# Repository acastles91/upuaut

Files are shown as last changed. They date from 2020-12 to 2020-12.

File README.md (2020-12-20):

# upuaut
Upuaut KiCad Project

### Explicación
El proyecto se abre desde el archivo `upuaut_2Nils.pro`. El esquemático correspondiente es `upuaut_2Nils.sch`. La nomenclatura es un desorden porque empecé a hacer el proyecto antes de saber de version control y no he reordenado todo, cuando sepa mejor por donde coger lo haré de ceros. 

En el esquemático se puede ver arriba a la izquierda el Teensy 3.2 que controla todo. Las conexiones están hechas sobre todo con `labels`. `START-STOP`, `DIRECTION-SWITCH`, `CAPTURE` y `SPEED-SELECT` son botones con interrupt. El código lo puede ver en [este repositorio](https://github.com/acastles91/Upu). El loop es en términos generales algo así:

```
volatile Request requestStream = checkInputStreamOF(Serial, prevRequest);
  if(requestStream != prevRequest){
    switchStateOF(requestStream,
                prevRequest, 
                stepperObj, 
                stepControlObj, 
                rotateControlObj, 
                sensorObj, 
                rotaryObj, 
                openCelluloidObj, 
                motorObj, 
                bounceSensor,
                leds,
                encoderObj,
                bounceEncoButton,
                triggerTimerObj,
                modeObj,
                debouncers,
                stateObj,
                bounceStartStop);
    prevRequest = requestStream;
  }

    volatile Request requestButton = checkInputButtonsOF(debouncers, prevRequest);
    if(requestButton != prevRequest){
    switchStateOF(requestButton,
                prevRequest,
                stepperObj, 
                stepControlObj, 
                rotateControlObj, 
                sensorObj, 
                rotaryObj, 
                openCelluloidObj, 
                motorObj, 
                bounceSensor,
                leds,
                encoderObj,
                bounceEncoButton,
                triggerTimerObj,
                modeObj,
                debouncers,
                stateObj,
                bounceStartStop);
     }
```
Escribí una clase que se llama `Request`. Las funciones `checkInputStreamOF()` y `checkInputButtonsOF()` tienen como `return value` un `Request`. Existe de antes un `Request` llamado `prevRequest`. Este `Request` es el valor del último `Request` del cual el programa tiene conocimiento. Si las funciones dan como `return value` algo diferente al `Request` anterior, o sea `prevRequest`, se llama la función `switchStateOF()`. Esta función cambia el estado de la máquina: la pone en movimiento, la frena, le cambia la velocidad etc. Lo fundamental es que este cambio de estado depende de la clase de `Request` que se haga, que se hace con los botones de la máquina en el caso de `checkInputButtonsOF()` o de paquetes a través del `Serial` en `checkInputStreamOF()`. Cuando hay un cambio de estado de los botones `checkInputButtonOF()` genera un `Request` distinto a `prevRequest`, y los botones tienen que tener interrupt para poder guardar este cambio de nuevo valor sin importar en qué momentodel loop suceda. 

Aparte de los botones, el Teensy tiene conectados distintos Leds que no son muy importantes para la funcionalidad. Otro punto central de la máquina es el `SENSOR`. Este sensor también tiene un `interrupt`. No recuerdo bien cómo lo solucioné en su momento, pero la idea es que el sensor de la máquina está posicionado enfrente del opturador del proyector y detecta si el opturador está o no abierto. El sensor tiene que detectar la posición del opturador independientemente de los pasos del motor. El sensor lee cambios de estado, de abierto a cerrado. Tiene que ser o 0 o 1. Todavía no estoy muy convencido del sensor que estoy usando pero eso lo podemos ver después.Cuando hay un cambio de estado el sensor le suma 1 a un contador. Cuando el contador llega a 4 el controlador manda un paquete serial al computador para que capture el frame y el contador vuelve a 0. El numero 4 tiene que ver con la forma física del opturador. Esta función de mandar el paquete tiene que ser inmediata, independiente del lugar del loop en que suceda. 

 Otro aspecto importante es el motor, que se controla con los pins `STEP`, `DIRECTION` y `ENABLE`. El modo `STEP/DIR` es relativamente sencillo, sólo se necesita que `STEP` sea capaz de `PWM` para que los pasos no interfieran con el loop. Si cambio de microcontrolador me toca encontrar librerías que manejen bien la aceleración y sean fáciles de usar. Creo que el `StepStick` debería tener un condensador en algún lugar y en el esquemátic no está. Quiero usar sobre todo controladores de Trinamics, en especial el [TMC5160] (https://www.trinamic.com/support/eval-kits/details/silentstepstick/). Para eso necesito conectarlo a por `SPI`, o sea me toca designar pins para `MISO`, `MOSI` y `CLK`. ¿Usted sabe si estos pins pueden ser cualquier pin o tienen que ser unos específicos? El `CHIP_SELECT` ya lo tengo asignado pero creo que nunca logré ponerlo en funcionamiento bien, terminé usando unos drivers que funcionan por `UART` pero que también se pueden usar por defecto en `Standalone Mode` y solo neceistan `STEP/DIR` si no se les da nada más. 

Otra funcionalidad que quedó por explorar es la que está ahi marcada como `SOUND`. El principio es que se pueda, en vez de mandar un paquete serial cada vez que hay un nuevo frame, generar un sonido y amplificarlo y mandarlo por un jack de 3.5 para conectarlo a una entrada de audio de una grabadora externa. El resultado sería un beep cada vez que haya un frame nuevo. `SHUTTER` es semejante pero para un opturador de una camara de fotos, a través de un optocoplador. 

Además de esto hay un ventilador que seguramente no funciona bien, unos reguladores de voltaje para bajar la entrade de 24V a 5V y 12V (creo que 5V sobra, la pienso cambiar a 3.3V), un Mosfet para proteger el sistema en caso de polaridad invertida y un LED muy poderoso que se controla directamente con un driver que está en el board pero que no está conectado con el microcontrolador sino que se regula con un potenciometro.

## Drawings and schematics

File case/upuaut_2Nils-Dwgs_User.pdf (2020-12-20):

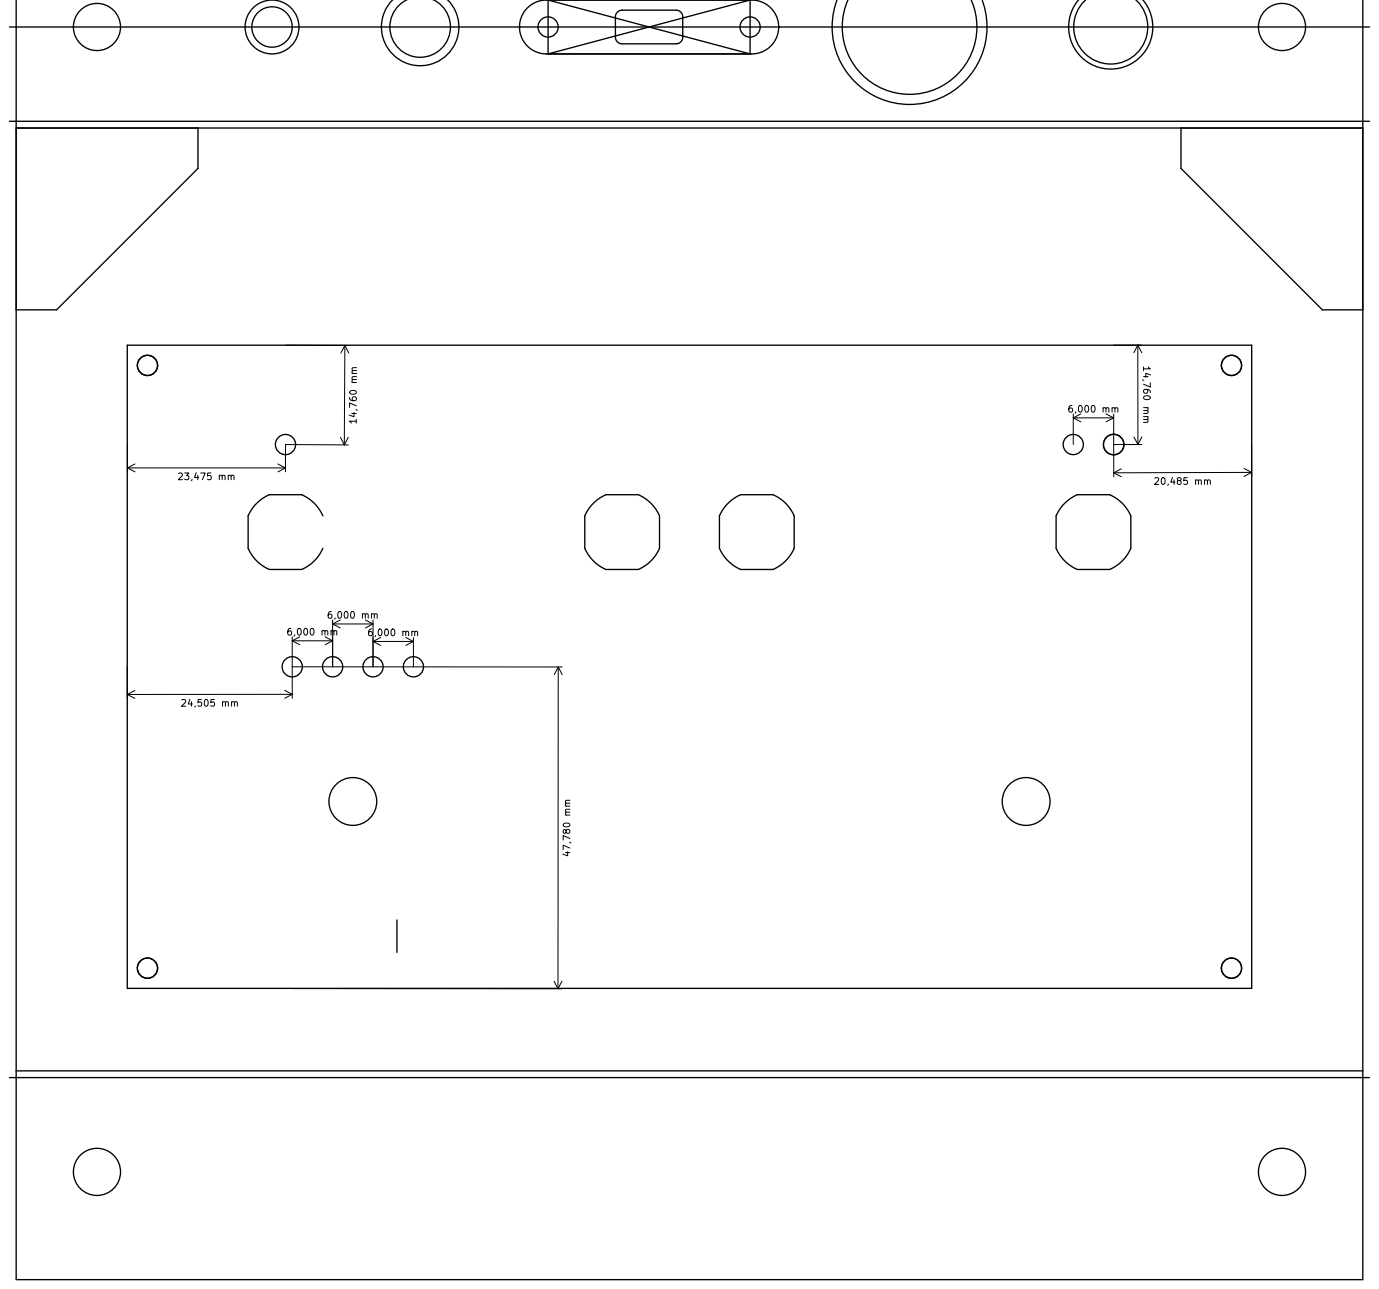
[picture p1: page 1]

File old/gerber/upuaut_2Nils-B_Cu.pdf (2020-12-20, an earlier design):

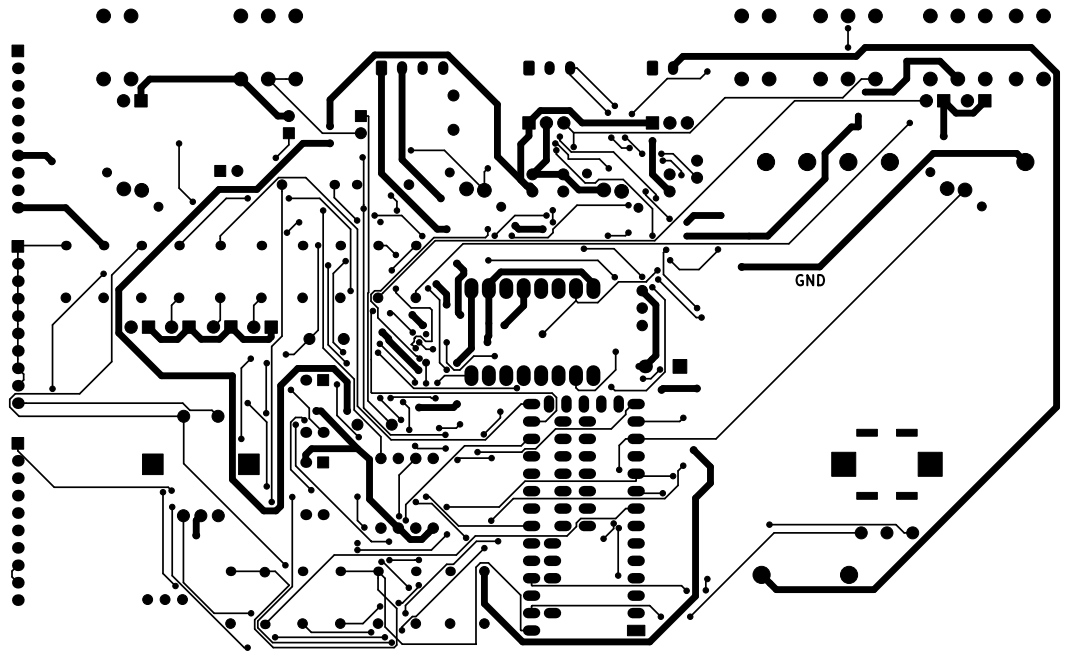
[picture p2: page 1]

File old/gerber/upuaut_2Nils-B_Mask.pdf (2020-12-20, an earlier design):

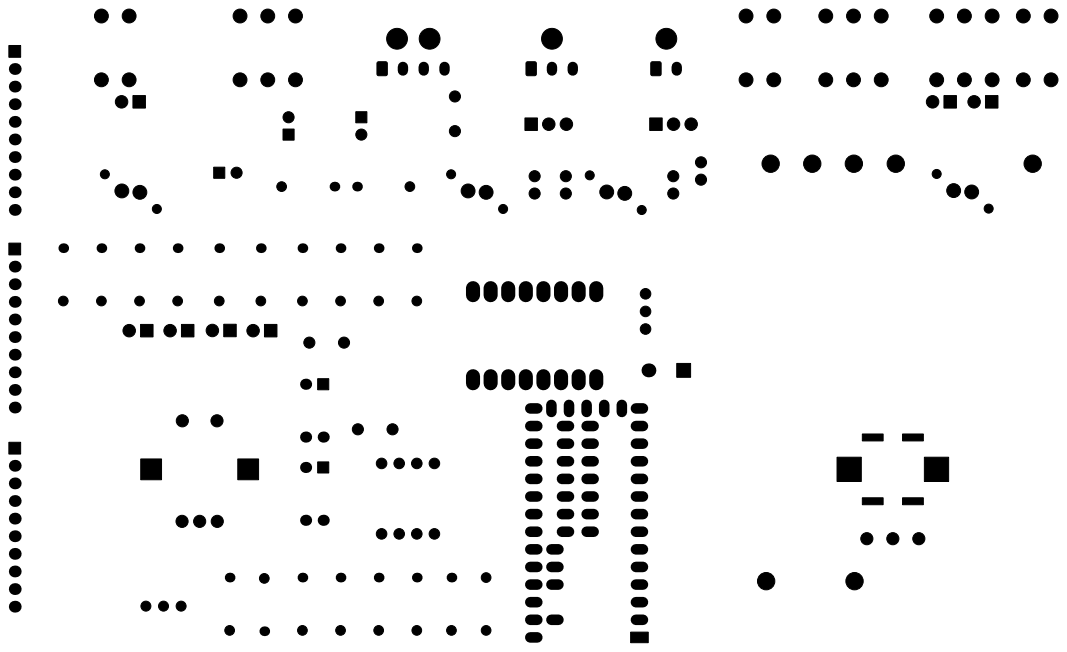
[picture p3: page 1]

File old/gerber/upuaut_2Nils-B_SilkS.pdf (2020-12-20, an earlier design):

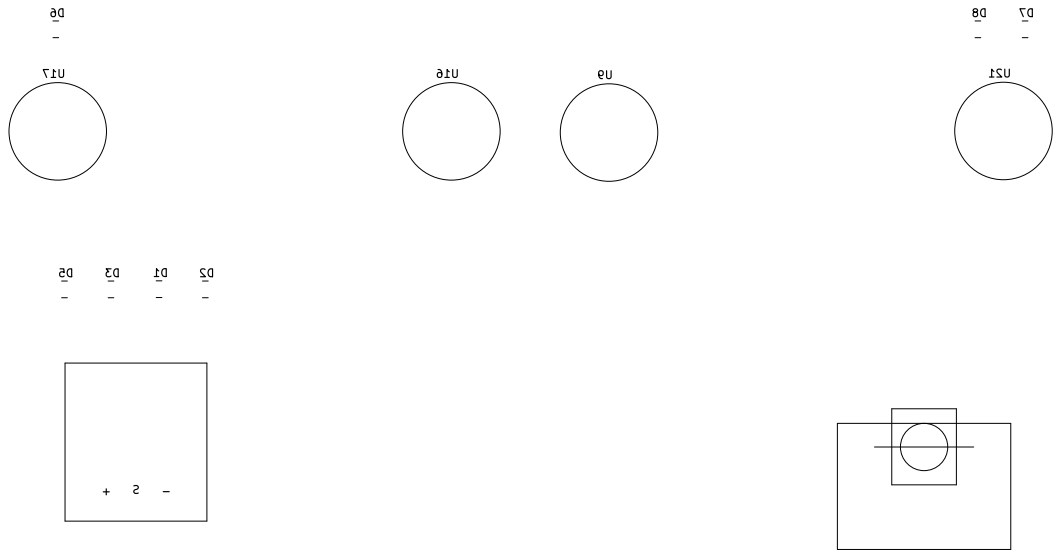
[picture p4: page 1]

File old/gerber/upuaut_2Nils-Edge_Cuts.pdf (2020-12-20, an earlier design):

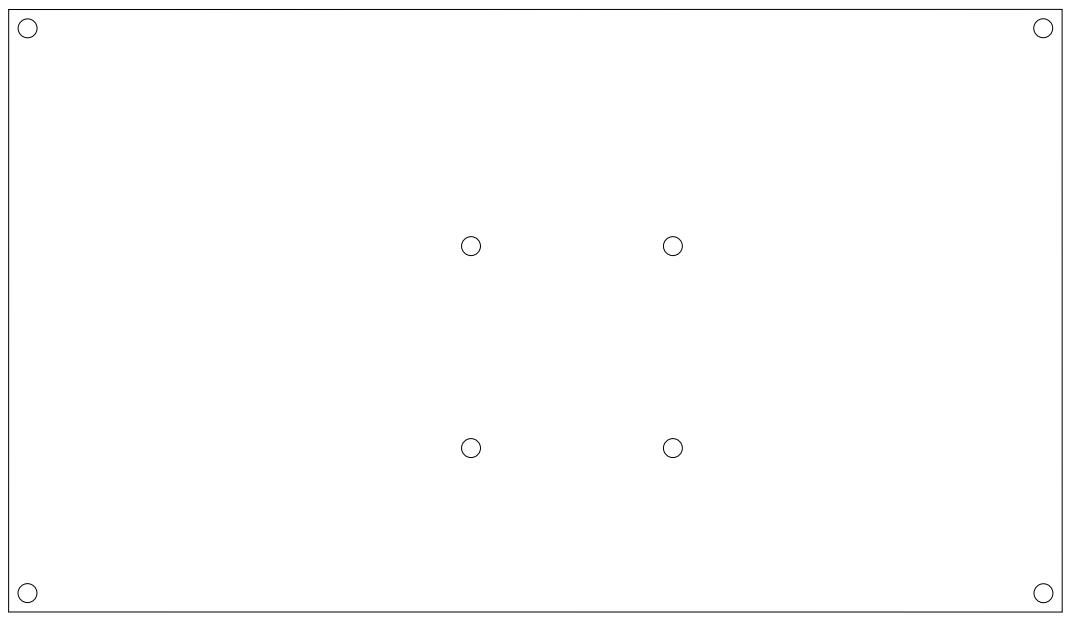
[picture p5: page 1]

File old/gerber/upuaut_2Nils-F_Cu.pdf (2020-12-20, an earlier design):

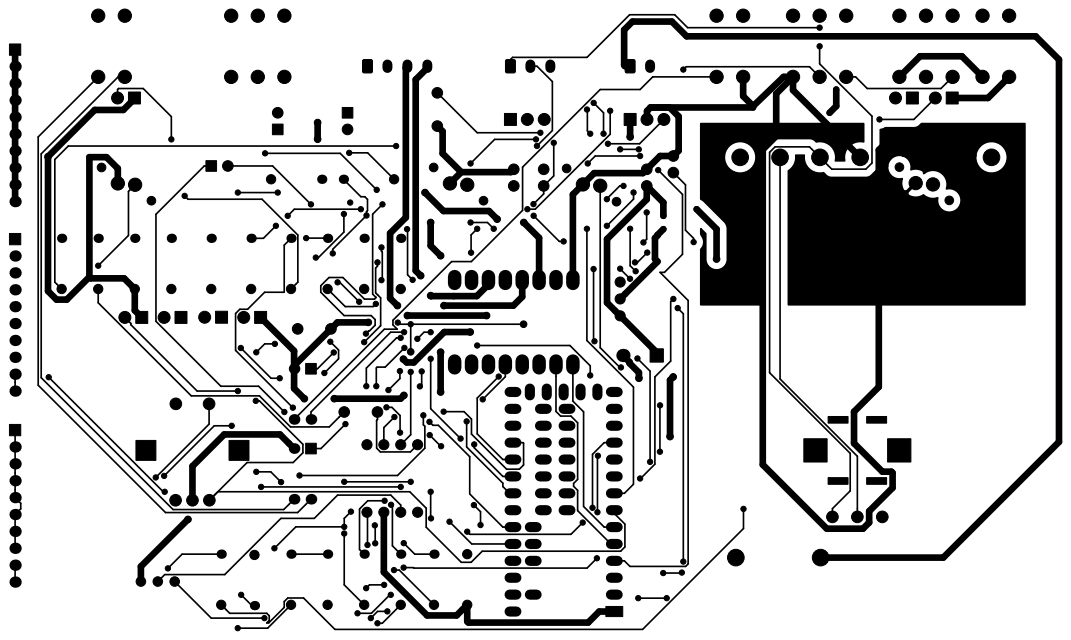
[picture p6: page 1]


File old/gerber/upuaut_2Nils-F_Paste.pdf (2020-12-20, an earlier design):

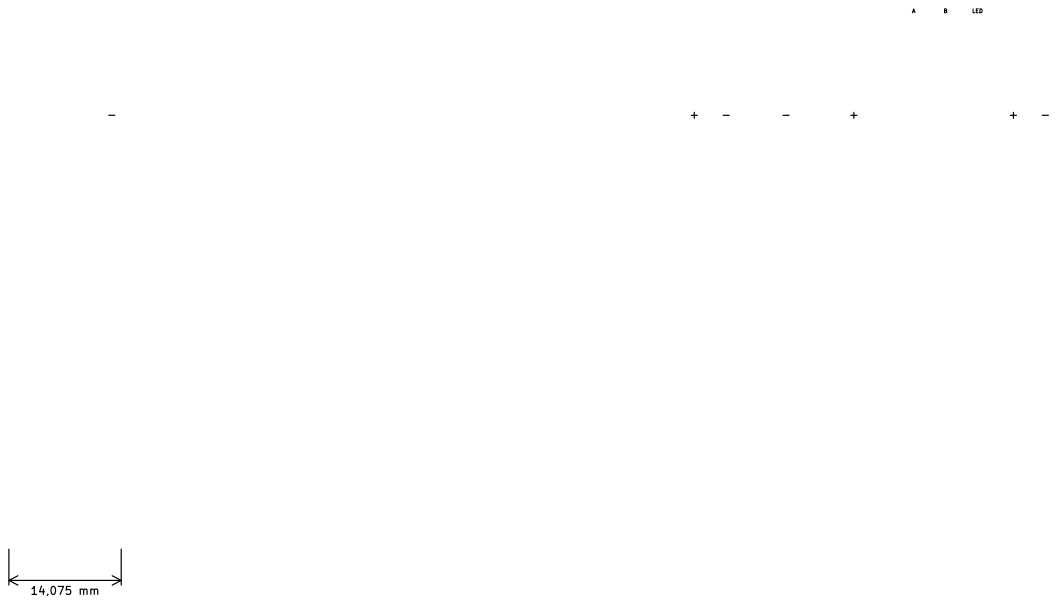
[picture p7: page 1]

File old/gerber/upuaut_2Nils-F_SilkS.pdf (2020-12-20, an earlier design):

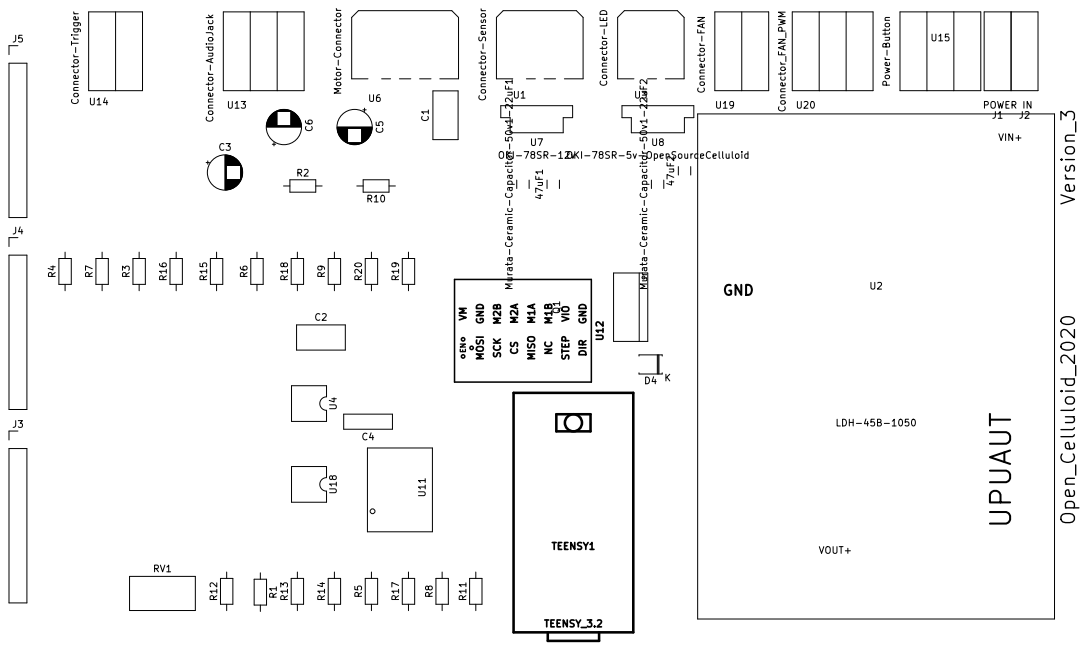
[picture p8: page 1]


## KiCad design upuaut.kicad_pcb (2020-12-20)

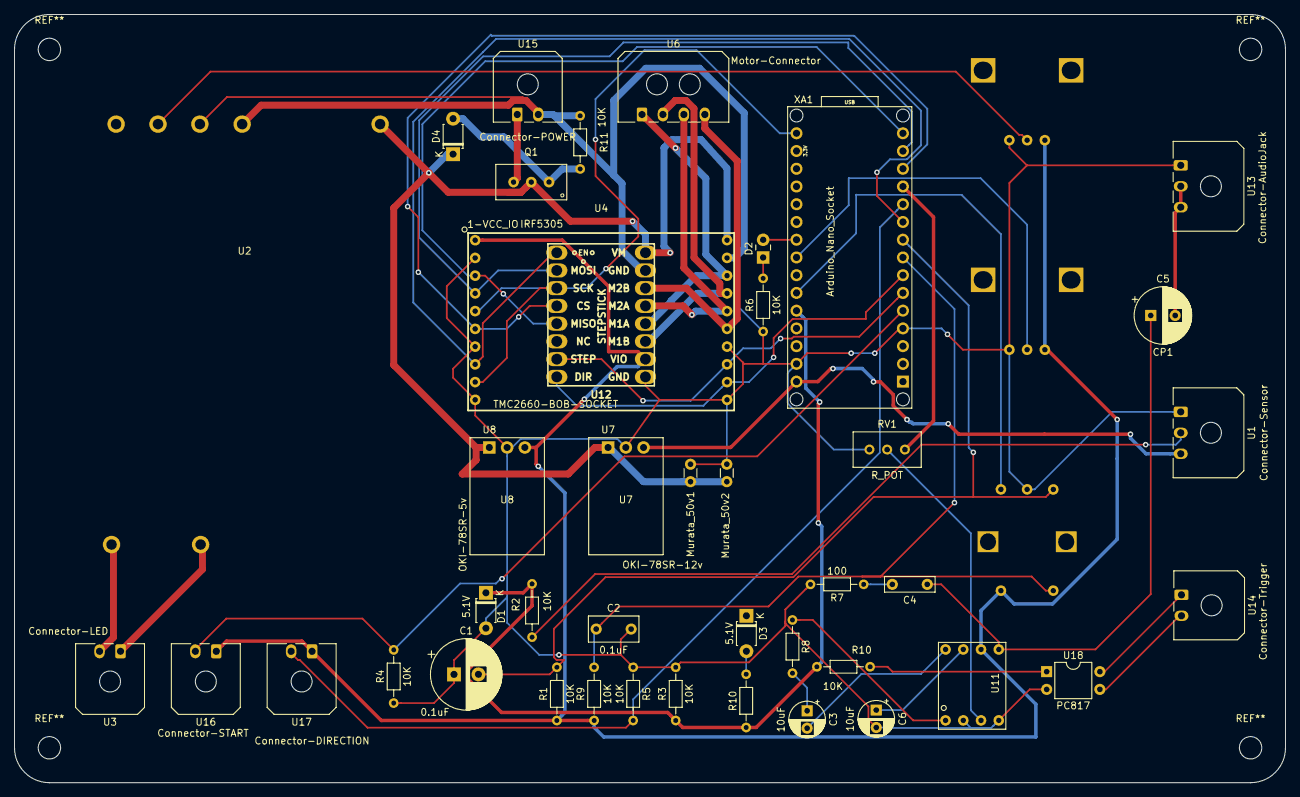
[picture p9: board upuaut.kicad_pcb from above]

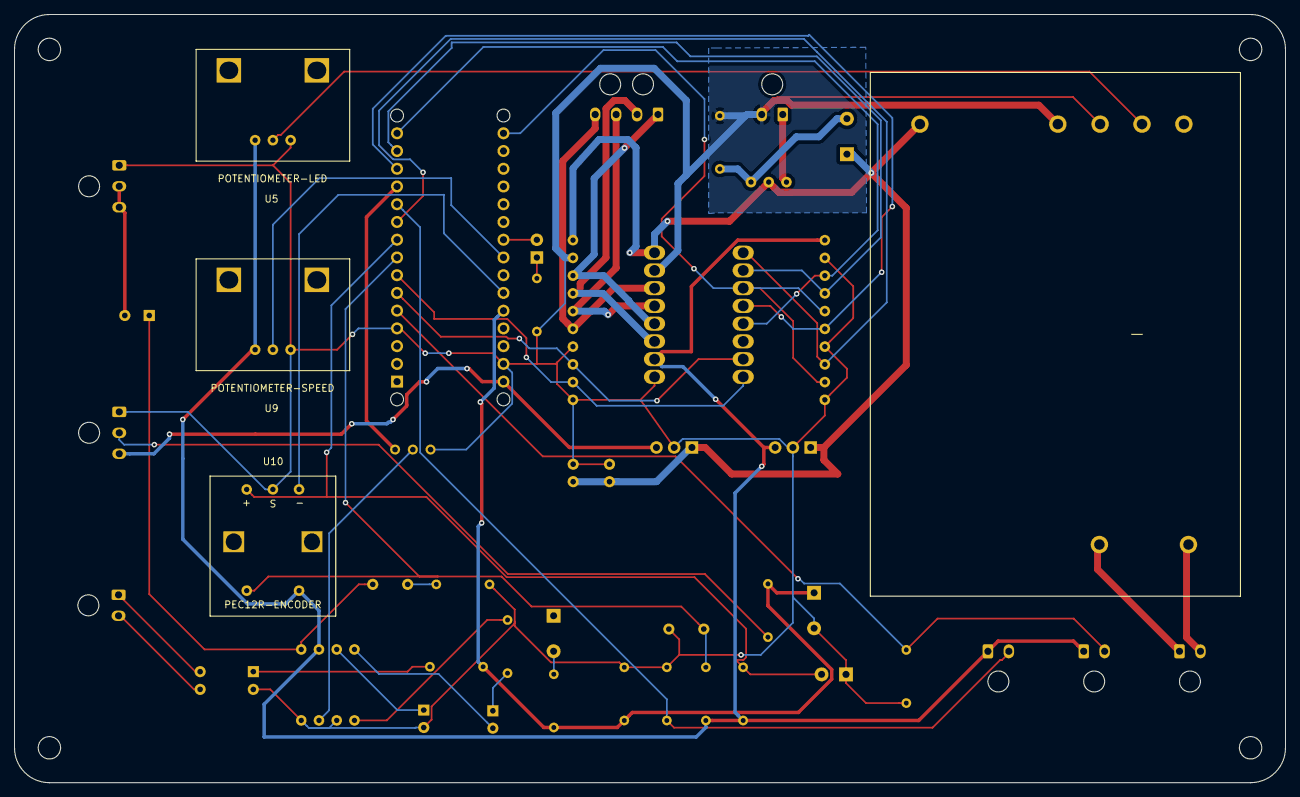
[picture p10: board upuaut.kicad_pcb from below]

Board: 2 copper layers, 182.0 x 110.0 mm, 45 parts (3 on the bottom side), 43 nets.

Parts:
C1: 0.1uF; CP_Radial_D10.0mm_P3.50mm
C2: 0.1uF; C_Rect_L7.0mm_W3.5mm_P5.00mm
C3, C6: 10uF; CP_Radial_D5.0mm_P2.50mm
C4: 10pF; C_Rect_L7.0mm_W2.0mm_P5.00mm
C5: CP1; CP_Radial_D8.0mm_P3.50mm
D1, D3: 5.1V; D_T-1_P5.08mm_Horizontal
D2: LED; LED_Rectangular_W3.0mm_H2.0mm
D4: 10,1V; D_T-1_P5.08mm_Horizontal
Murata_50v1, Murata_50v2: C; C_Disc_D3.0mm_W1.6mm_P2.50mm
Q1: IRF5305
R1, R2, R3, R4, R5, R6, R9, R10#2, R11: 10K; R_Axial_DIN0204_L3.6mm_D1.6mm_P7.62mm_Horizontal
R7: 100; R_Axial_DIN0204_L3.6mm_D1.6mm_P7.62mm_Horizontal
R8, R10: R; R_Axial_DIN0204_L3.6mm_D1.6mm_P7.62mm_Horizontal
RV1: R_POT; Potentiometer_Bourns_3296W_Vertical
U1: Connector-Sensor; Molex_Micro-Fit_3.0_43650-0300_1x03_P3.00mm_Horizontal
U2: LDH-45B-1050; MeanWell-LDH-45B-1050
U3: Connector-LED; Molex_Micro-Fit_3.0_43650-0200_1x02_P3.00mm_Horizontal
U4: TMC2660-BOB-SOCKET; TMC2660-BOB
U5: POTENTIOMETER-LED; PDB12-H4301-Potentiometer
U6: Motor-Connector; Molex_Micro-Fit_3.0_43650-0400_1x04_P3.00mm_Horizontal
U7: OKI-78SR-12v; Converter_DCDC_muRata_OKI-78SR_Horizontal
U8: OKI-78SR-5v; Converter_DCDC_muRata_OKI-78SR_Horizontal
U9: POTENTIOMETER-SPEED; PDB12-H4301-Potentiometer
U10: PEC12R-ENCODER; Potentiometer-BOURNS
U11: LM386
U12: STEPSTICK
U13: Connector-AudioJack; Molex_Micro-Fit_3.0_43650-0300_1x03_P3.00mm_Horizontal
U14: Connector-Trigger; Molex_Micro-Fit_3.0_43650-0200_1x02_P3.00mm_Horizontal
U15: Connector-POWER; Molex_Micro-Fit_3.0_43650-0200_1x02_P3.00mm_Horizontal
U16: Connector-START; Molex_Micro-Fit_3.0_43650-0200_1x02_P3.00mm_Horizontal
U17: Connector-DIRECTION; Molex_Micro-Fit_3.0_43650-0200_1x02_P3.00mm_Horizontal
U18: PC817; DIP-4_W7.62mm
XA1: Arduino_Nano_Socket

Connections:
5V: R1.1, R9.1, U4.1, U5.1, U8.3, U9.1, U10.4, U11.6, U12.15, U16.1, U17.1
12V: U1.3, U7.3, XA1.VIN
24V: D4.1, Murata_50v1.1, Murata_50v2.1, Q1.1, U2.5, U4.20, U7.1, U8.1, U12.9
+24V: Q1.8, U15.1
AUDIO-SIGNAL: C5.2, U13.2, U13.3
BLACK: U4.15, U6.4, U12.11
BLUE: U4.17, U6.2, U12.14
CHANNEL-A: C1.2, R1.2, U10.1, XA1.D6
CHANNEL-B: C2.1, R9.2, U10.5, XA1.D5
CHIP-SELECT: U4.6, U12.5, XA1.D10
CLOCK: U4.5, U4.9, U12.6, XA1.D13
DIRECTION: U4.12, U12.1, XA1.D4
DIRECTION-SWITCH: R5.2, U17.2, XA1.D8
ENABLE: U4.8, U12.8, XA1.D7
ENCO-BUTTON: U10.3, XA1.A6
GND: C1.1, C2.2, C6.2, D1.2, Murata_50v1.2, Murata_50v2.2, R3.2, R4.1, R5.1, R6.1, R7.2, R11.1, RV1.3, U1.1, U2.3, U2.4, U4.2, U4.7, U4.10, U4.11, U4.14, U4.19, U5.3, U7.2, U8.2, U9.3, U10.2, U11.2, U11.4, U12.10, U12.16, U13.1, U15.2, U18.2, XA1.GND1, XA1.GND2
GREEN: U4.16, U6.3, U12.12
LED: D2.2, XA1.A3
LED+: U2.7, U3.1
LED-: U2.6, U3.2
MISO-SDO: U4.3, U12.4, XA1.D12
MOSI-SDI: U4.4, U12.7, XA1.D11
unnamed: C3.1, R8.2
unnamed: C3.2, U11.8
unnamed: C4.1, C5.1, U11.5
unnamed: C4.2, R7.1
unnamed: C6.1, U11.7
unnamed: D2.1, R6.2
unnamed: D3.2, R10.2
unnamed: D4.2, Q1.4, R11.2
unnamed: R2.1, U1.2
unnamed: R8.1, U11.1
unnamed: R10#2.2, U18.1
unnamed: RV1.2, U11.3
unnamed: U14.1, U18.4
unnamed: U14.2, U18.3
POTI-LED: U2.2, U5.2
POTI-SPEED: U9.2, XA1.A4
RED: U4.18, U6.1, U12.13
SHUTTER: D1.1, R2.2, R3.1, R10.1, R10#2.1, XA1.A7
SOUND-TRIGGER: RV1.1, XA1.D9
START-STOP: R4.2, U16.2, XA1.D2
STEP: U4.13, U12.2, XA1.D3

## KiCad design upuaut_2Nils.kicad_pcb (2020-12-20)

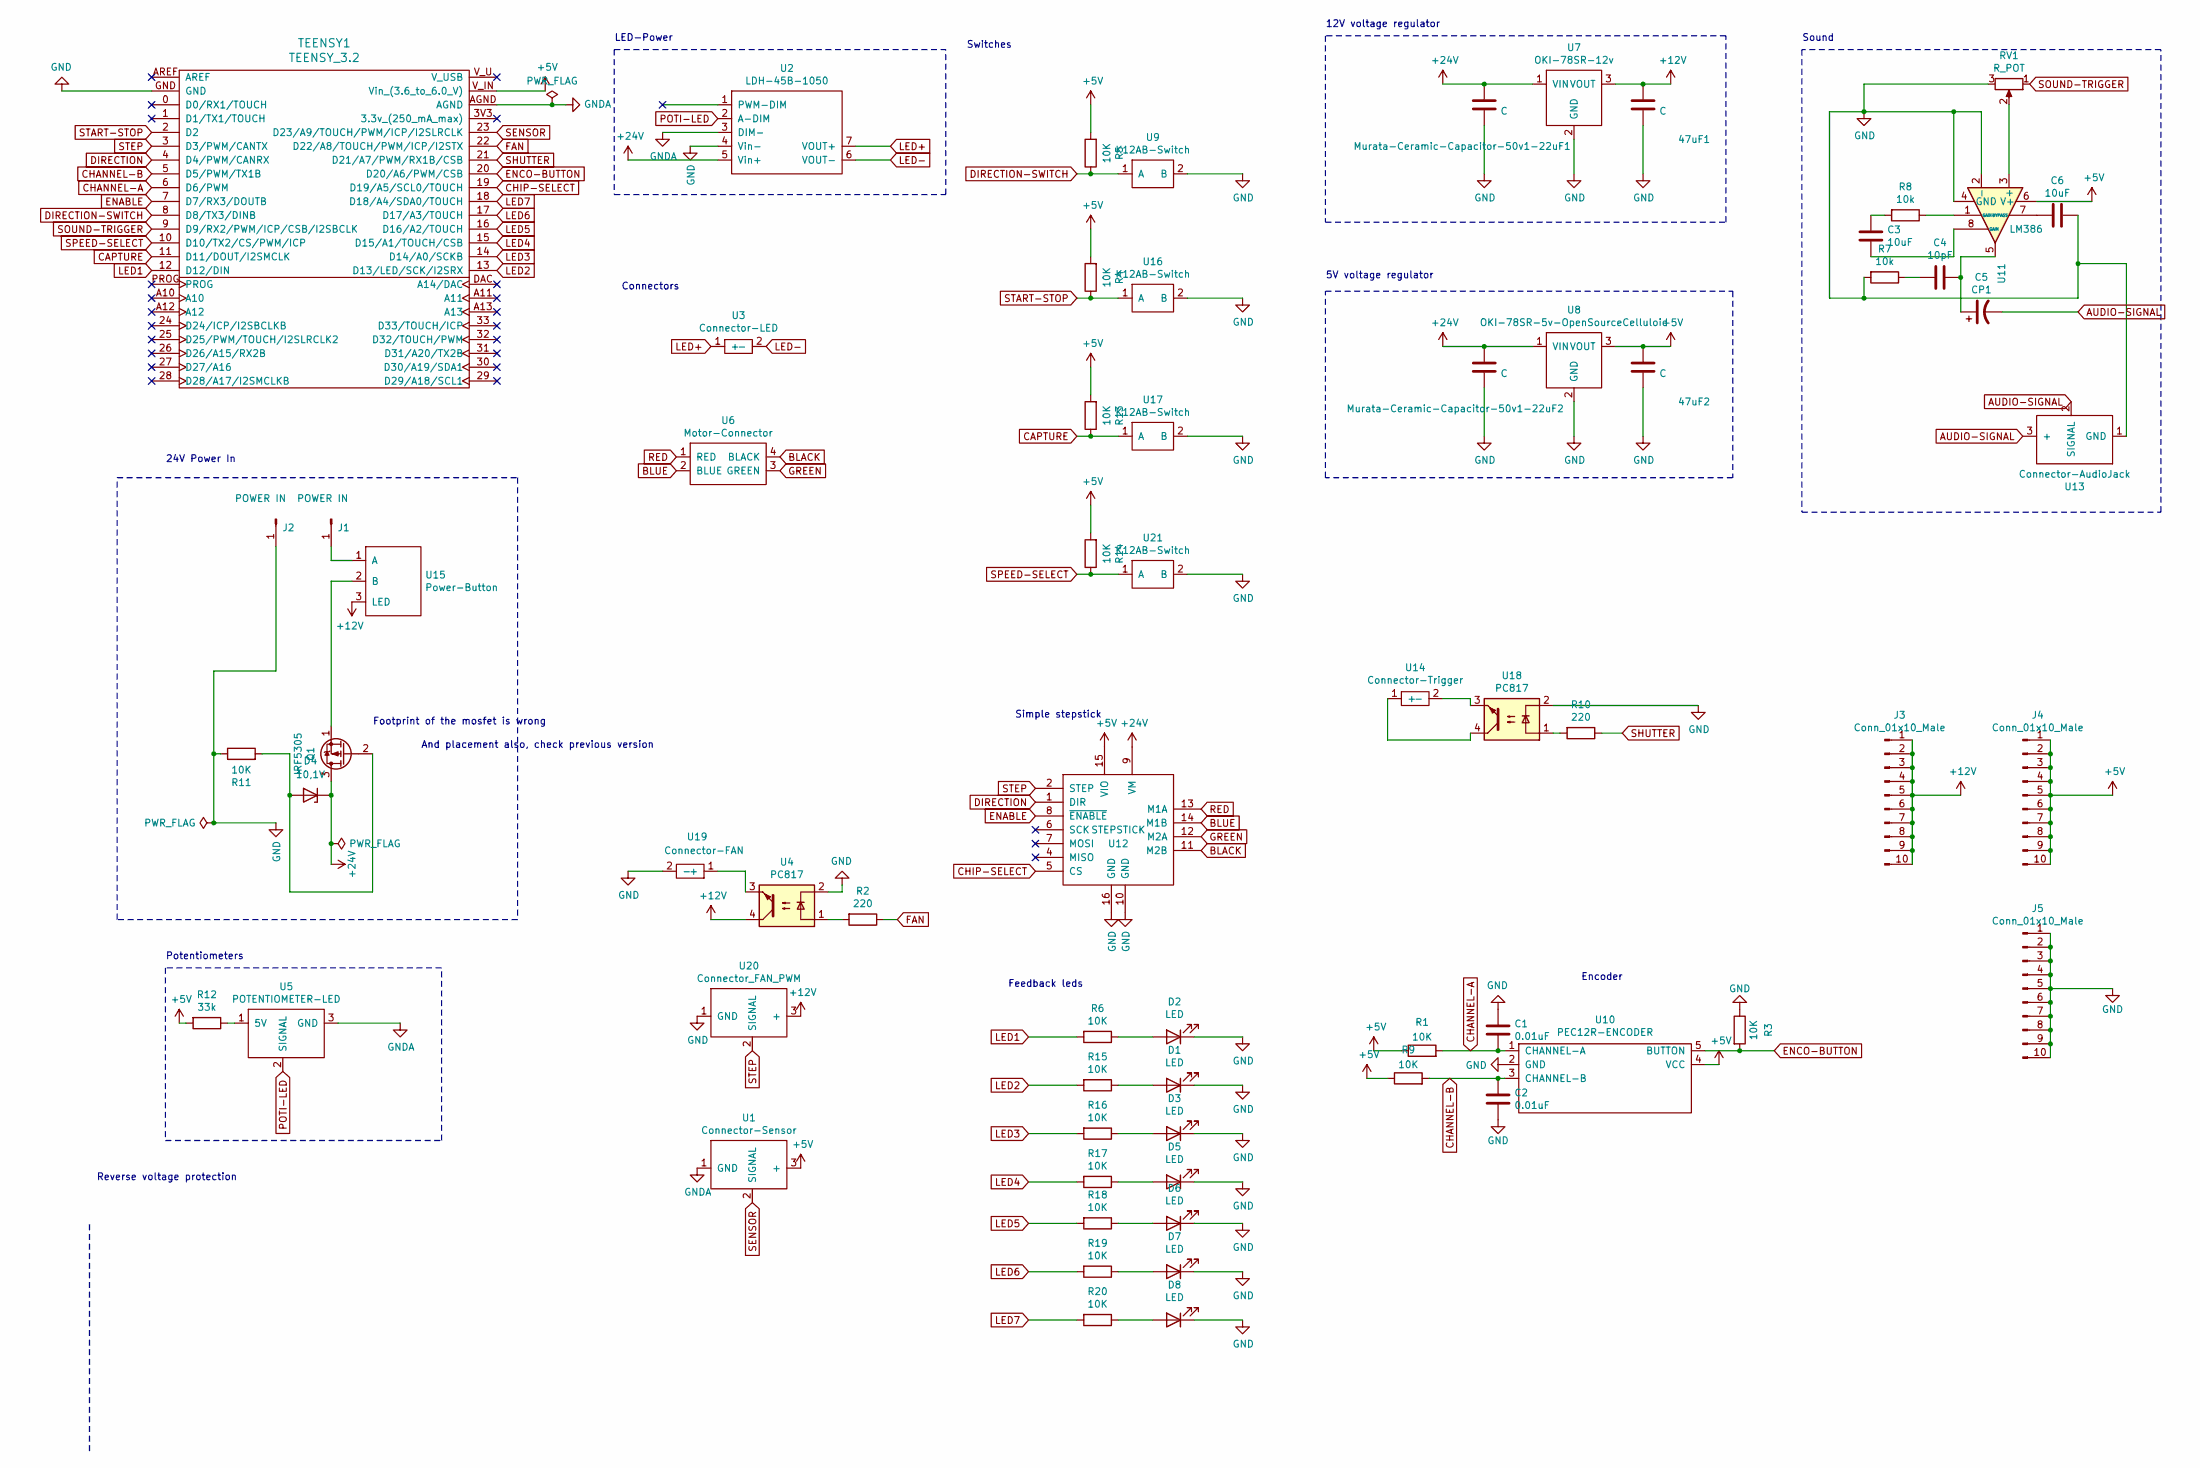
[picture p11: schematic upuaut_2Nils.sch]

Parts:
47uF1, 47uF2: C; C_Disc_D3.0mm_W1.6mm_P2.50mm
C1, C2: 0.01uF; C_Rect_L7.0mm_W3.5mm_P5.00mm
C3, C6: 10uF; CP_Radial_D5.0mm_P2.50mm
C4: 10pF; C_Rect_L7.0mm_W2.0mm_P5.00mm
C5: CP1; CP_Radial_D5.0mm_P2.50mm
D1, D2, D3, D5, D6, D7, D8: LED; LED_Rectangular_W3.0mm_H2.0mm
D4: 10,1V; D_T-1_P5.08mm_Horizontal
J1, J2: POWER IN; WAGO_PCB_Klemme_1Pol
J3, J4, J5: Conn_01x10_Male; PinHeader_1x10_P2.54mm_Vertical
Murata-Ceramic-Capacitor-50v1-22uF1, Murata-Ceramic-Capacitor-50v1-22uF2: C; C_Disc_D3.0mm_W1.6mm_P2.50mm
Q1: IRF5305
R1, R3, R4, R5, R6, R9, R11, R13, R14, R15, R16, R17, R18, R19, R20: 10K; R_Axial_DIN0204_L3.6mm_D1.6mm_P7.62mm_Horizontal
R2, R10: 220; R_Axial_DIN0204_L3.6mm_D1.6mm_P7.62mm_Horizontal
R7, R8: 10k; R_Axial_DIN0204_L3.6mm_D1.6mm_P7.62mm_Horizontal
R12: 33k; R_Axial_DIN0204_L3.6mm_D1.6mm_P7.62mm_Horizontal
RV1: R_POT; Potentiometer_Bourns_3296W_Vertical
TEENSY1: TEENSY_3.2
U1: Connector-Sensor; Molex_Micro-Fit_3.0_43650-0300_1x03_P3.00mm_Horizontal
U2: LDH-45B-1050; MeanWell-LDH-45B-1050
U3: Connector-LED; Molex_Micro-Fit_3.0_43650-0200_1x02_P3.00mm_Horizontal
U4, U18: PC817; DIP-4_W7.62mm
U5: POTENTIOMETER-LED; PDB12-H4301-Potentiometer
U6: Motor-Connector; Molex_Micro-Fit_3.0_43650-0400_1x04_P3.00mm_Horizontal
U7: OKI-78SR-12v; Converter_DCDC_muRata_OKI-78SR_Vertical
U8: OKI-78SR-5v-OpenSourceCelluloid; Converter_DCDC_muRata_OKI-78SR_Vertical
U9, U16, U17, U21: K12AB-Switch
U10: PEC12R-ENCODER; Potentiometer-BOURNS
U11: LM386
U12: STEPSTICK
U13: Connector-AudioJack; WAGO_PCB_Klemme_3Pol
U14: Connector-Trigger; WAGO_PCB_Klemme_2Pol
U15: Power-Button; WAGO_PCB_Klemme_3Pol
U19: Connector-FAN; WAGO_PCB_Klemme_2Pol
U20: Connector_FAN_PWM; WAGO_PCB_Klemme_3Pol

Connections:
+5V: 47uF2.1, J4.1, J4.2, J4.3, J4.4, J4.5, J4.6, J4.7, J4.8, J4.9, J4.10, R1.1, R4.2, R5.2, R9.1, R12.2, R13.2, R14.2, TEENSY1.V_IN (Vin_(3.6_to_6.0_V)), U1.3 (+), U8.3 (VOUT), U10.4 (VCC), U11.6 (V+), U12.15 (VIO)
+12V: 47uF1.1, J3.1, J3.2, J3.3, J3.4, J3.5, J3.6, J3.7, J3.8, J3.9, J3.10, U4.4, U7.3 (VOUT), U15.3 (LED), U20.3 (+)
+24V: D4.1 (K), Murata-Ceramic-Capacitor-50v1-22uF1.1, Murata-Ceramic-Capacitor-50v1-22uF2.1, Q1.3 (D), U2.5 (Vin+), U7.1 (VIN), U8.1 (VIN), U12.9 (VM)
AUDIO-SIGNAL: C5.2, U13.2 (SIGNAL), U13.3 (+)
BLACK: U6.4 (BLACK), U12.11 (M2B)
BLUE: U6.2 (BLUE), U12.14 (M1B)
CAPTURE: R13.1, TEENSY1.11 (D11/DOUT/I2SMCLK), U17.1 (A)
CHANNEL-A: C1.2, R1.2, TEENSY1.6 (D6/PWM), U10.1 (CHANNEL-A)
CHANNEL-B: C2.1, R9.2, TEENSY1.5 (D5/PWM/TX1B), U10.3 (CHANNEL-B)
CHIP-SELECT: TEENSY1.19 (D19/A5/SCL0/TOUCH), U12.5 (CS)
DIRECTION: TEENSY1.4 (D4/PWM/CANRX), U12.1 (DIR)
DIRECTION-SWITCH: R5.1, TEENSY1.8 (D8/TX3/DINB), U9.1 (A)
ENABLE: TEENSY1.7 (D7/RX3/DOUTB), U12.8 (~ENABLE)
ENCO-BUTTON: R3.2, TEENSY1.20 (D20/A6/PWM/CSB), U10.5 (BUTTON)
FAN: R2.1, TEENSY1.22 (D22/A8/TOUCH/PWM/ICP/I2STX)
GND: 47uF1.2, 47uF2.2, C1.1, C2.2, C6.2, D1.1 (K), D2.1 (K), D3.1 (K), D5.1 (K), D6.1 (K), D7.1 (K), D8.1 (K), J2.1, J5.1, J5.2, J5.3, J5.4, J5.5, J5.6, J5.7, J5.8, J5.9, J5.10, Murata-Ceramic-Capacitor-50v1-22uF1.2, Murata-Ceramic-Capacitor-50v1-22uF2.2, R3.1, R7.2, R11.1, RV1.3, TEENSY1.GND, U2.4 (Vin-), U4.2, U7.2 (GND), U8.2 (GND), U9.2 (B), U10.2 (GND), U11.2 (-), U11.4 (GND), U12.10 (GND), U12.16 (GND), U13.1 (GND), U16.2 (B), U17.2 (B), U18.2, U19.2 (-), U20.1 (GND), U21.2 (B)
GNDA: TEENSY1.AGND, U1.1 (GND), U2.3 (DIM-), U5.3 (GND)
GREEN: U6.3 (GREEN), U12.12 (M2A)
LED1: R6.2, TEENSY1.12 (D12/DIN)
LED2: R15.2, TEENSY1.13 (D13/LED/SCK/I2SRX)
LED3: R16.2, TEENSY1.14 (D14/A0/SCKB)
LED4: R17.2, TEENSY1.15 (D15/A1/TOUCH/CSB)
LED5: R18.2, TEENSY1.16 (D16/A2/TOUCH)
LED6: R19.2, TEENSY1.17 (D17/A3/TOUCH)
LED7: R20.2, TEENSY1.18 (D18/A4/SDA0/TOUCH)
LED+: U2.7 (VOUT+), U3.1 (+)
LED-: U2.6 (VOUT-), U3.2 (-)
unnamed: C3.1, R8.2
unnamed: C3.2, U11.8 (GAIN)
unnamed: C4.1, C5.1, U11.5
unnamed: C4.2, R7.1
unnamed: C6.1, U11.7 (BYPASS)
unnamed: D1.2 (A), R15.1
unnamed: D2.2 (A), R6.1
unnamed: D3.2 (A), R16.1
unnamed: D4.2 (A), Q1.2 (G), R11.2
unnamed: D5.2 (A), R17.1
unnamed: D6.2 (A), R18.1
unnamed: D7.2 (A), R19.1
unnamed: D8.2 (A), R20.1
unnamed: J1.1, U15.1 (A)
unnamed: Q1.1 (S), U15.2 (B)
unnamed: R2.2, U4.1
unnamed: R8.1, U11.1 (GAIN)
unnamed: R10.2, U18.1
unnamed: R12.1, U5.1 (5V)
unnamed: RV1.2, U11.3 (+)
unnamed: U14.1 (+), U18.4
unnamed: U14.2 (-), U18.3
unnamed: U4.3, U19.1 (+)
POTI-LED: U2.2 (A-DIM), U5.2 (SIGNAL)
RED: U6.1 (RED), U12.13 (M1A)
SENSOR: TEENSY1.23 (D23/A9/TOUCH/PWM/ICP/I2SLRCLK), U1.2 (SIGNAL)
SHUTTER: R10.1, TEENSY1.21 (D21/A7/PWM/RX1B/CSB)
SOUND-TRIGGER: RV1.1, TEENSY1.9 (D9/RX2/PWM/ICP/CSB/I2SBCLK)
SPEED-SELECT: R14.1, TEENSY1.10 (D10/TX2/CS/PWM/ICP), U21.1 (A)
START-STOP: R4.1, TEENSY1.2 (D2), U16.1 (A)
STEP: TEENSY1.3 (D3/PWM/CANTX), U12.2 (STEP), U20.2 (SIGNAL)

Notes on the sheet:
Reverse voltage protection
Sound
Encoder
12V voltage regulator
5V voltage regulator
Feedback leds
Switches
Simple stepstick
Potentiometers
LED-Power
Connectors
24V Power In
Footprint of the mosfet is wrong
And placement also, check previous version

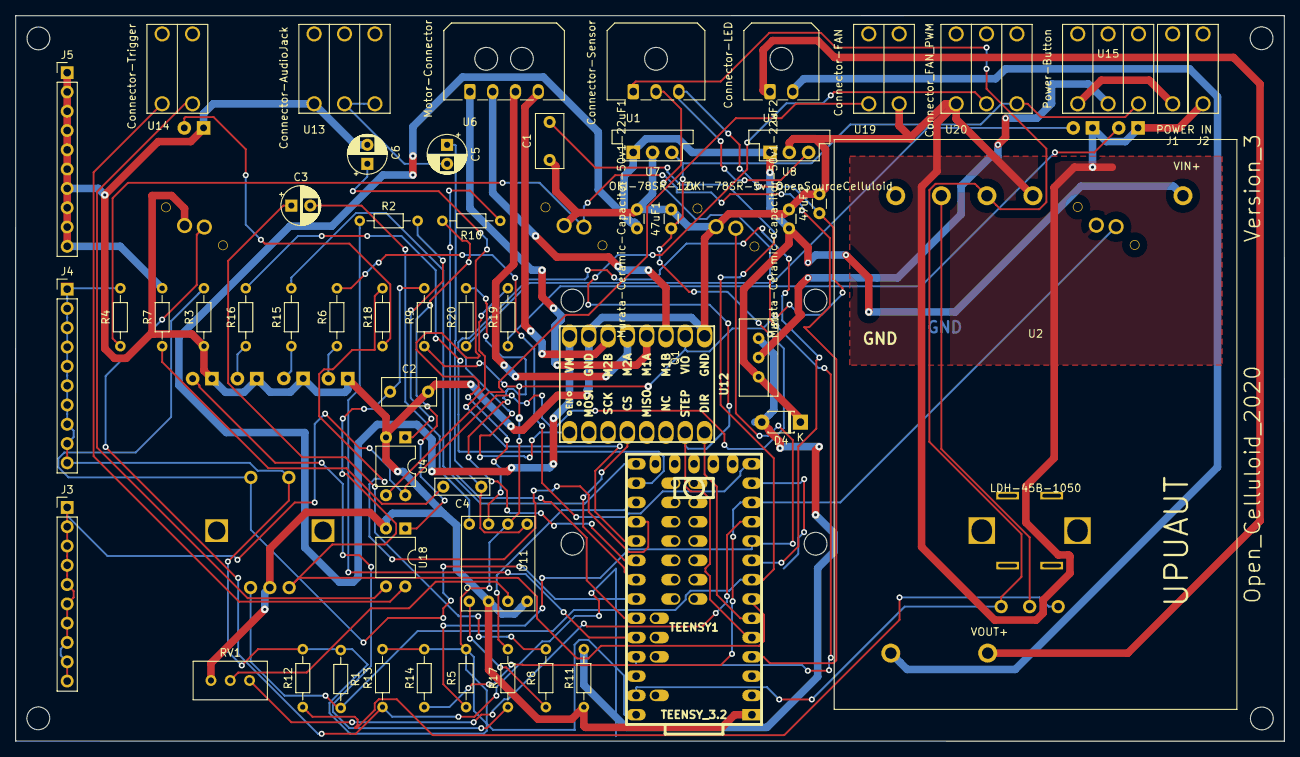
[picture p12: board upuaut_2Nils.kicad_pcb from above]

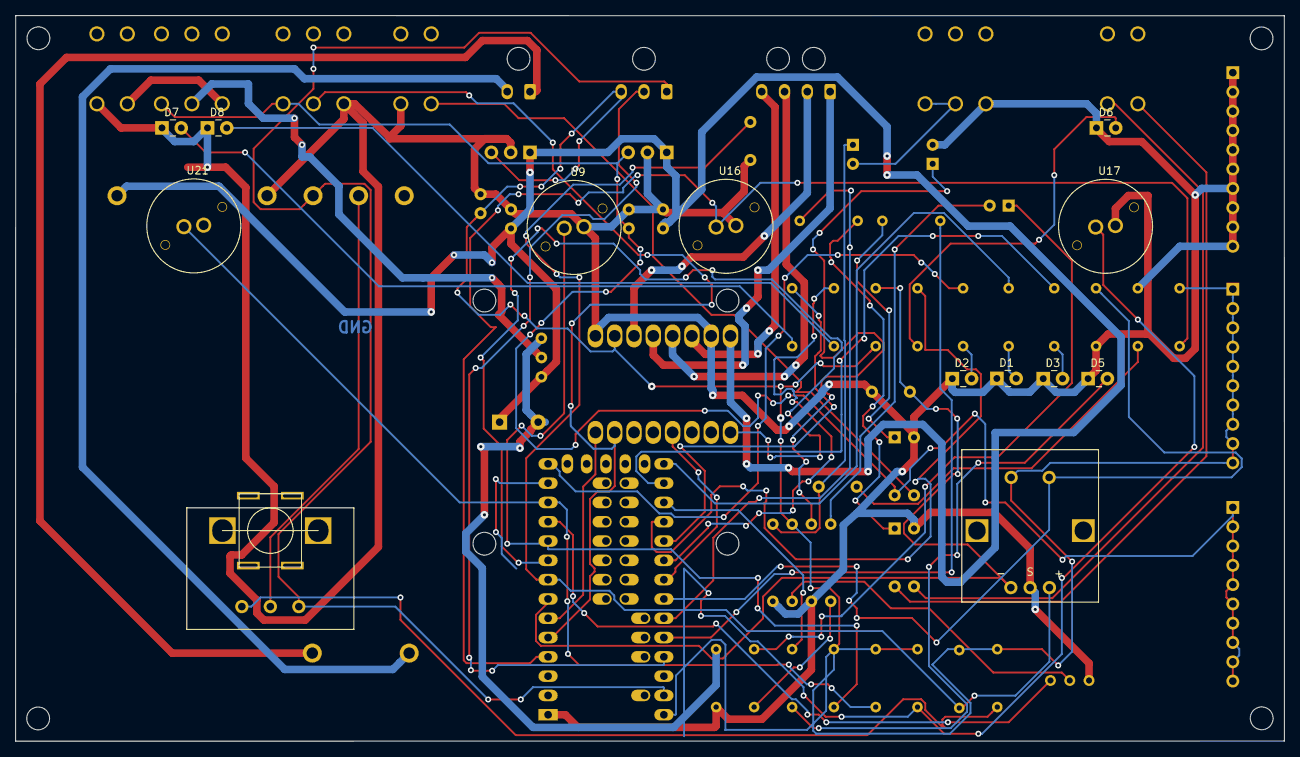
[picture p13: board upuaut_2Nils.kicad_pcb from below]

Board: 2 copper layers, 167.0 x 95.5 mm, 67 parts (13 on the bottom side), 58 nets.
